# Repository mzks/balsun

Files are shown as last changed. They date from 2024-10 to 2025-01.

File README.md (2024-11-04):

# balsun - Balloon adaptive link board with Wi-SUN

This is an arduino-compatible board for balloon experiments.

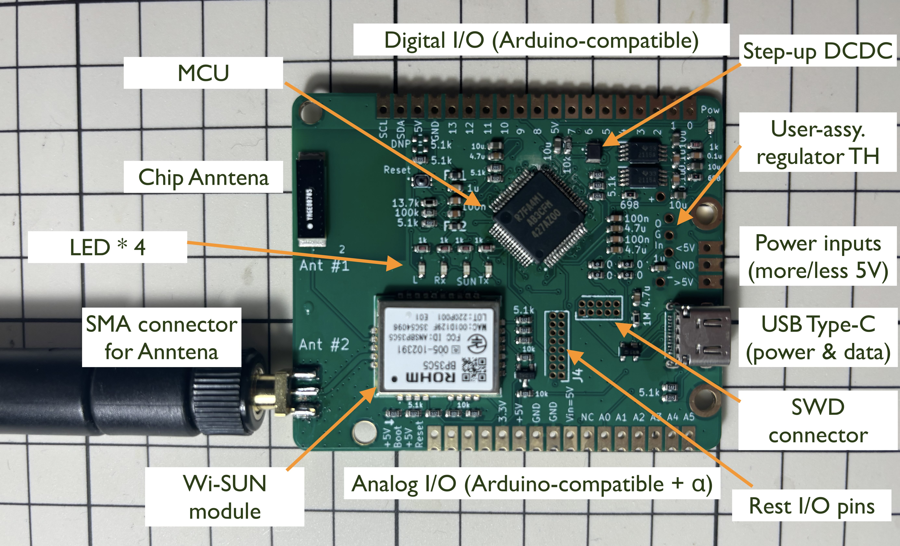
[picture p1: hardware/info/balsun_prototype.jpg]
Balsun prototype photo


## Features

 - Arduino UNO R4 Minima-compatible hardware
 - Low EMC noise for general balloon RF system
 - Wi-SUN FAN communication (MIC/TELEC, FCC)
 - Open hardware and software

## Specifications

 - MCU Renesas RA4M1
 - 5V IOs (GPIO, UART, SCI, I2C, CAN, ADC, DAC, OpAmp) with castellated holes
 - Write bootloader/sketch/program via USB type-C
 - Multi power sources (1.5--5V) and more (users can mount their regurator via through holes)
 - PCB size is 64.5 * 53.4 mm, FR-4 1.6 mm
 - Wi-SUN with BP35C5 (RoHM) and two types of the anntena

## How can I get?

All hardware design is published as KiCAD files.
You can ask some manifactures to build them.
If you are customer of JLCPCB, Elecrow, FusionPCB, or PCBWay, you can find the zip files including everything to build PCB in [here](/hardware/info/gerber_to_order).
For PCBA, BOM and Pos files are [here](/hardware/info).
All parts are available in Mouser (2024 Oct. 24).

## Contact
Keita Mizukoshi (mizukoshi.keita@jaxa.jp)

## Local information
Japanese specific information and discussion among local balloon community in [jp-docs](/docs/jp-docs.md).

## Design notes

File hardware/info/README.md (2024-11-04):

# Hardware design documents

  - [Circuit diabram / 回路図](circuit_diagram.pdf) -- pdf内マウスオーバーで詳細情報あり
  - [BOM / 部品リスト](BOM_grouped.csv)
  - [Gerber files to order / PCB製造業者毎のガーバーファイルなど](gerber_to_order)

  - [ボードのイメージ図](board_top.png)
  - [部品リスト(未グループ化)](BOM.csv)
  - [部品位置 (top)](balsun-top.pos)
  - [部品位置 (bottom)](balsun-bottom.pos) -- 下側に実装するSMDはなし
  - [Simple CAD model / ボードのCADモデル](cad_model.step)
  - [P板.comに依頼した際の部品調達書](BOM_pban.xlsx)

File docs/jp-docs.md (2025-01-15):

# Balsun 国内向け情報

## Balsun
Balsun - Balloon adaptive link board with Wi-SUN は, 大気球実験向けに作ったWi-SUNチップを搭載したArduino UNO R4 Minima 互換ボードです.
大気球実験PIが, 地上系/搭載系で簡単に用いることができる汎用ボードとして開発されています.
なお, 開発者や開発者の所属機関が性能を保証する性質のものではありません.

## 今後
現在アルファ版作成の準備として製作業者の選定, 依頼を進めています.

## Getting started
Arduinoとして使う方法を説明します.
これらは, 試験用の仮の方法であり, 将来的に更新される予定です.

### ブートローダーの書き込み
[こちら](https://zenn.dev/ichirowo/articles/6aa1614e102bce) も参考になります.

まずは, USBの接続状態を確認できるツールをインストールします.
例えば, [USB Device Tree Viewer](https://www.uwe-sieber.de/usbtreeview_e.html) が利用できます.

次に, [Renesas Flash Programmer](https://www.renesas.com/jp/ja/software-tool/renesas-flash-programmer-programming-gui#overview) をダウンロード, インストールします.

最後に, [Arduino IDE](https://www.arduino.cc/en/software) をインストールして, Arduino UNO R4 Minimaのための設定をしておきます.

Balsun基板の, Boot pin (左下から2番目) とGNDをショートして, USB type-C経由でコンピューターと接続します.
その後, Resetボタンをおす (または, Reset pinとGNDのショート) と, デバイスが認識されます.
USB Device Tree Viewerに, RA USB Boot(CDC)(COMxx) などと表示されます.

Renesas Flash Programmerを起動して, ファイル→新しいプロジェクトを作成を選択し, マイクロコントローラにRA, COM portに確認したポートを指定します. その他は適当に入力してください.
または, "Connect Settings" タブからToolに COM port, Speedに115200 bps, Tool Details... に確認したCOMポートを指定します.

プログラムファイルの「参照」をクリックし、UNO R4 MINIMAのブートローダーを指定します。以下のフォルダから、「`dfu_minima.hex`」を指定します。
`C:\Users\<ユーザー名>\AppData\Local\Arduino15\packages\arduino\hardware\renesas_uno\1.0.1\bootloaders\SANTIAGO`
もしくは
`C:\Users\<ユーザー名>\AppData\Local\Arduino15\packages\arduino\hardware\renesas_uno\1.0.2\bootloaders\UNO_R4`

スタートボタンをおすと, 書き込みが始まります. 緑色で"操作が成功しました"と表示されたら完了です.

その後, Arduino IDEを開いて, 適当なスケッチを書き込めが, Arduinoとして認識されるはずです.

### Wi-SUNチップの利用

以下のスケッチをMaster, Slaveにそれぞれ書き込みます.

 - master
 ```
UART SerialX(23,24);

void setup() {

  pinMode(LED_BUILTIN, OUTPUT);
  Serial.begin(9600); // USB type-C
  SerialX.begin(115200, SERIAL_8N1); // Serial pin for Wi-SUN
    
  R_IOPORT_PinCfg(NULL, BSP_IO_PORT_02_PIN_04, IOPORT_CFG_PORT_DIRECTION_OUTPUT);

  R_IOPORT_PinWrite(NULL, BSP_IO_PORT_02_PIN_04, BSP_IO_LEVEL_HIGH);
  delay(100);
  R_IOPORT_PinWrite(NULL, BSP_IO_PORT_02_PIN_04, BSP_IO_LEVEL_LOW);
  delay(100);
  R_IOPORT_PinWrite(NULL, BSP_IO_PORT_02_PIN_04, BSP_IO_LEVEL_HIGH);
  delay(100);
  SerialX.println ("atstart BORDER");
  delay(100);
  SerialX.println("save");
  delay(100);
  SerialX.println("vernum");
  delay(10000);
  SerialX.println("rantsw 1"); // 1 for chip, 2 for SMA
  delay(100);

  digitalWrite(LED_BUILTIN, HIGH);
  //if (SerialX.available() > 0){
  //  String msg = SerialX.readString();
  //  Serial.print(msg);
  //} 
}

const int adc_pin = A5;
int counter = 0;

void loop() {
  if (Serial.available() > 0){
    String cmd = Serial.readString();
    SerialX.print(cmd);
  }
  if (SerialX.available() > 0){
    String msg = SerialX.readString();
    Serial.print(msg);
  } 

  counter++;

  delay(100);
}

 ```

 - slave
 ```
 UART SerialX(23, 24);

int split(String data, char delimiter, String* dst) {
  int index = 0;
  int arraySize = (sizeof(data)) / sizeof((data[0]));
  int datalength = data.length();

  for (int i = 0; i < datalength; i++) {
    char tmp = data.charAt(i);
    if (tmp == delimiter) {
      index++;
      if (index > (arraySize - 1)) return -1;
    } else dst[index] += tmp;
  }
  return (index + 1);
}

int pin2_counter = 0;
int pin3_counter = 0;
int pin4_counter = 0;

void setup() {

  pinMode(2, OUTPUT);
  pinMode(3, OUTPUT);
  pinMode(4, OUTPUT);

  Serial.begin(9600); // USB type-C

  SerialX.begin(115200, SERIAL_8N1); // Serial pin for Wi-SUN

  R_IOPORT_PinCfg(NULL, BSP_IO_PORT_02_PIN_04, IOPORT_CFG_PORT_DIRECTION_OUTPUT);

  R_IOPORT_PinWrite(NULL, BSP_IO_PORT_02_PIN_04, BSP_IO_LEVEL_HIGH);
  delay(100);
  R_IOPORT_PinWrite(NULL, BSP_IO_PORT_02_PIN_04, BSP_IO_LEVEL_LOW);
  delay(100);
  R_IOPORT_PinWrite(NULL, BSP_IO_PORT_02_PIN_04, BSP_IO_LEVEL_HIGH);
  delay(100);

  delay(10000);
  SerialX.println("rantsw 1"); // 1 for chip, 2 for SMA
}

int counter = 0;
const int adc_pin = A5;

void loop() {
  if (Serial.available() > 0){
    String cmd = Serial.readString();
    SerialX.print(cmd);
  }

  if (SerialX.available() > 0){
    String msg = SerialX.readString();
    Serial.print(msg);

    int idx = msg.indexOf("tcpr");

    if(idx == 1){
      String buf[10];
      split(msg, ' ', buf);
      int cmdid = buf[2].toInt();

      if(cmdid==1){
          Serial.print("debug command");
          SerialX.println("tcps 2001:db8::1 0000");
      } else if (cmdid==2){
        SerialX.println("tcps 2001:db8::1 0002");
        pin2_counter = 300;
        digitalWrite(2, HIGH);
      } else if (cmdid==3){
        SerialX.println("tcps 2001:db8::1 0003");
        pin3_counter = 300;
        digitalWrite(3, HIGH);
      } else if (cmdid==4){
        SerialX.println("tcps 2001:db8::1 0004");
        pin4_counter = 100;
        digitalWrite(4, HIGH);
      } else if (cmdid==9){
        pin2_counter = 0;
        pin3_counter = 0;
        pin4_counter = 0;
        digitalWrite(4, HIGH);
      } else if (cmdid==9999){
          digitalWrite(2, HIGH);
          digitalWrite(3, HIGH);
          digitalWrite(4, HIGH);
          delay(10000);
          digitalWrite(2, LOW);
          digitalWrite(3, LOW);
          digitalWrite(4, LOW);
      }
    }

  }
  if (pin2_counter>0){pin2_counter--;} else {digitalWrite(2, LOW);}
  if (pin3_counter>0){pin3_counter--;} else {digitalWrite(3, LOW);}
  if (pin4_counter>0){pin4_counter--;} else {digitalWrite(4, LOW);}

  if (counter % 1000 == 999){
    int adc = analogRead(adc_pin);
    char sendPacket[24] = "";
    sprintf(sendPacket, "tcps 2001:db8::1 %04d", adc);
    SerialX.println(sendPacket);
    counter = 0;
  }

  counter++;
  delay(100);
}

 ```

書き込んだら, slaveの電源を投入し, masterはusbでコンピューターに接続してシリアルモニタを開きます.
ボーレートは9600です. (Source codeをいじれば適当に変えられます.)

```
atstart BORDER
```
とすると, response `atstart 1(BORDER)` が帰ってくるはずです.
これで, 設定をRAMに書き込むために, `save` と書き込むと, `save parameter is saved` とResponseが帰ってくるはずなので,
`reset` を打ってWi-SUNのチップの再立ち上げをします.
以下の出力が見えるはずです.
```
18:44:34.164 -> reset delay 0sec
18:44:34.164 -> inf 01,01,0,0       {    WSN: system booted.                      }
18:44:34.164 ->
////////////////////////////////////////////////////////////
18:44:34.164 -> // Copyright (C) 2020 Nissin Systems Co.,Ltd.
18:44:34.164 -> // EW-WSN-FAN-1.0.56.60 ROHM BP35C5(ROHM ML7436N:ML7421)
18:44:34.164 -> // Wi-SUN Profile for FAN (Dec 24 2020 12:55:57)
18:44:34.164 -> ////////////////////////////////////////////////////////////
18:44:34.164 -> auto start 1 (BORDER)...
18:44:34.164 -> init 1(BORDER)
18:44:34.164 -> inf 2b,62,0,5       {   FMng: changed fan join state (0 -> 5)     }
```

しばらく待つと, Slave機器を認識して, addressを与えます.

```
18:44:34.164 -> >inf 40,2b,bb48,4f5  {   NBRS: added new neighbor <001d129f35c54096>}
nebr <001d129f35c54096>: 256/127(-47)	<::>
18:45:07.166 -> >
inf 40,2d,3f7f,bb48 {   NBRS: added address <2001:db8::a9> to <001d129f35c54096>}
18:45:22.104 -> >
inf 4c,39,9d8c,9d60 {    RPL: added node <2001:db8::a9> => <2001:db8::1>}

```
その後, SlaveはADCの値を読んで定期的にMasterと通信してくるので,
```
tcpr <2001:db8::a9> 0040
18:47:14.445 -> >
tcpr <2001:db8::a9> 0040
18:48:55.375 -> >
tcpr <2001:db8::a9> 0040
18:50:36.343 -> >
tcpr <2001:db8::a9> 0041
18:52:17.342 -> >
```
以下のような出力が見えるはずです.

コマンドの詳細はdocumentを参照してください.
将来的にはWrapperを準備するつもりです.

また, 上でslaveのアドレスを確認したら, Masterから通信することもできます.
例えば,
```
tcps 2001:db8::a9 0000
```
などとすると, ScriptにしたがってResponseがあるはずです.

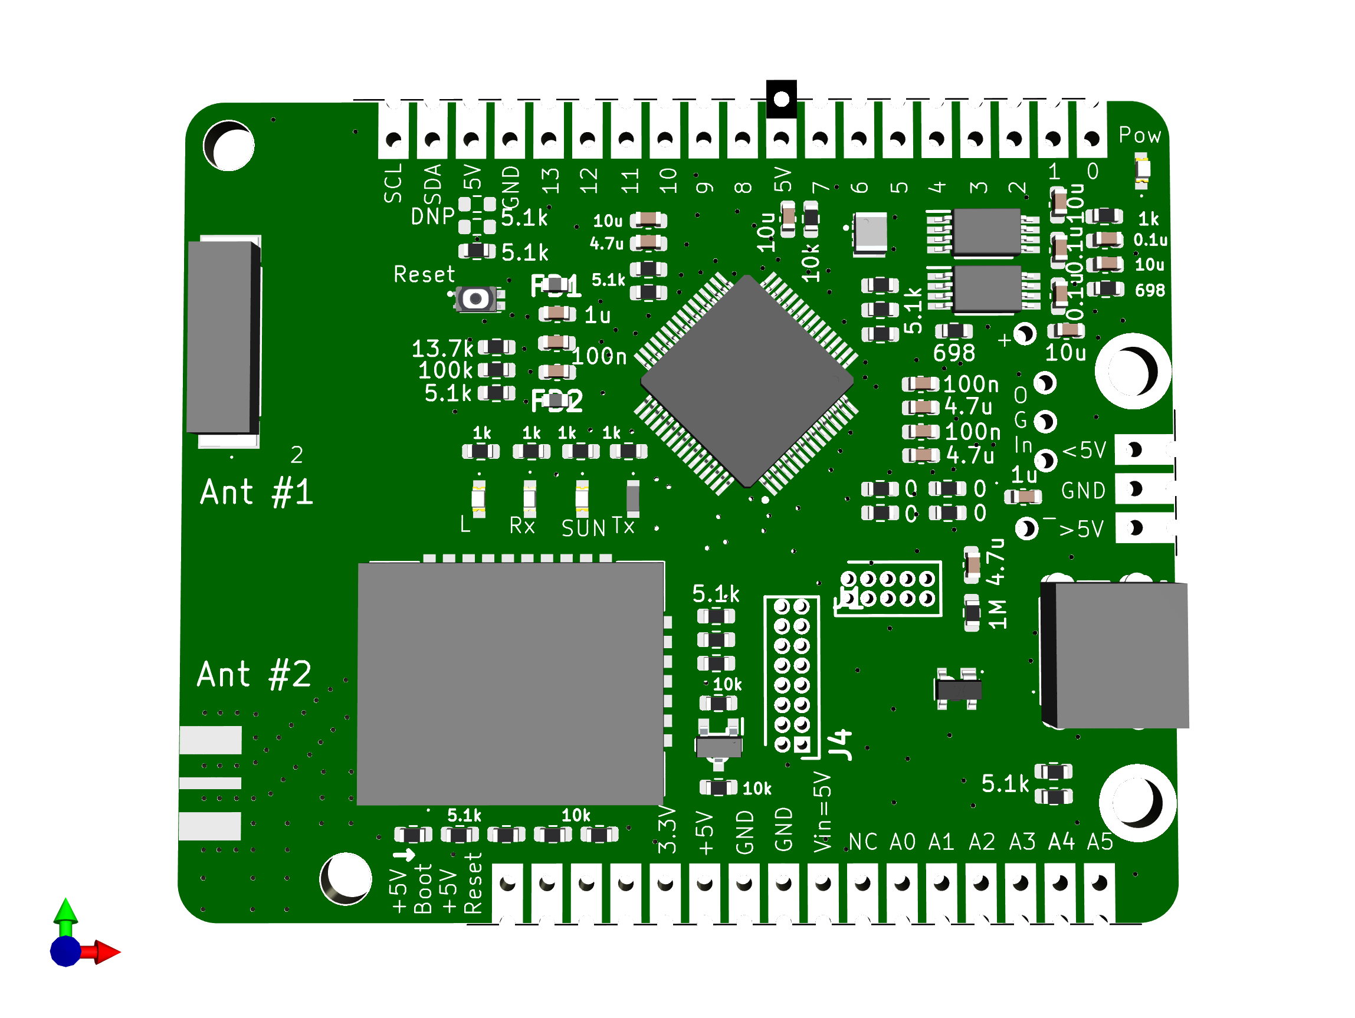
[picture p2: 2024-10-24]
hardware/info/board_top.png

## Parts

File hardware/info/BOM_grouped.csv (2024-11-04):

Reference | Value | Datasheet | Footprint | Qty | DNP | Manufacturer_Name | Manufacturer_Part_Number | Mouser Part Number | Mouser Price/Stock
ANT1 | ANT1204F005R0915A | https://eu.mouser.com/datasheet/2/447/datasheet_pulse_915mhz_1204_chip_antenna_type05_an-2903025.pdf | ANT1204F005R0915A | 1 |  | Pulse Electronics | ANT1204F005R0915A | 603-ANT1204F005R0915 | https://www.mouser.co.uk/ProductDetail/PulseLarsen-Antennas/ANT1204F005R0915A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
C1,C14 | 1u | ~ | Capacitor_SMD:C_0603_1608Metric | 2 |  |  |  | 603-CC603KRX5R6BB105
C2,C5,C7,C8 | 100n | ~ | Capacitor_SMD:C_0603_1608Metric | 4 |  |  |  | 603-CC603KRX7R6BB104
C3,C6,C9,C10 | 4.7u | ~ | Capacitor_SMD:C_0603_1608Metric | 4 |  |  |  | 603-CC603ZRY5V6BB475
C4,C11,C12,C13,C16 | 10u | ~ | Capacitor_SMD:C_0603_1608Metric | 5 |  |  |  | 603-CC603MRX6S6BB106
C15,C17,C18 | 0.1u | ~ | Capacitor_SMD:C_0603_1608Metric | 3 |  |  |  | 603-CC603KRX7R6BB104
D1 | PRTR5V0U2X,215 | https://assets.nexperia.com/documents/data-sheet/PRTR5V0U2X.pdf | PRTR5V0U2X | 1 |  | Nexperia | PRTR5V0U2X,215 | 771-PRTR5V0U2X-T/R | https://www.mouser.co.uk/ProductDetail/Nexperia/PRTR5V0U2X215?qs=LOCUfHb8d9sDkgY4cRj8Lw%3D%3D
FB1,FB2 | BLM18PG471SN1D | http://www.murata.com/~/media/webrenewal/support/library/catalog/products/emc/emifil/c31e.ashx?la=en-gb | BLM18SP221SN1B | 2 |  | Murata Electronics | BLM18PG471SN1D | 81-BLM18PG471SN1D | https://www.mouser.co.uk/ProductDetail/Murata-Electronics/BLM18PG471SN1D?qs=EYzdjubb4S%2FN1Ip39GrHyg%3D%3D
H1,H2,H3,H4,H5,P1 | ~ |  | -- mixed values -- | 6 | DNP
IC1 | R7FA4M1AB3CFM#AA0 | https://www.renesas.com/document/dst/renesas-ra4m1-group-datasheet?language=en&r=1054146 | QFP50P1200X1200X170-64N | 1 |  | Renesas Electronics | R7FA4M1AB3CFM#AA0 | 968-7FA4M1AB3CFM#AA0 | https://www.mouser.co.uk/ProductDetail/Renesas-Electronics/R7FA4M1AB3CFMAA0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
IC2 | BP35C5 | https://fscdn.rohm.com/en/products/databook/datasheet/module/power_module/specified_low_power/bp35c5-e.pdf | BP35C5 | 1 |  | ROHM Semiconductor | BP35C5 | 755-BP35C5
IC3 | BP5293-50 | https://componentsearchengine.com/Datasheets/2/MC7805BDTRKG.pdf | SamacSys_Parts:BP5293-50 | 1 | DNP |  |  |  | https://www.mouser.co.uk/ProductDetail/onsemi/MC7805BDTRKG?qs=%252B9%2Fcbd0IE0RVSCV5SBH6%2FA%3D%3D
IC4 | XCL103D503CR-G | https://www.torexsemi.com/file/xcl102/XCL102-103.pdf | XCL103D503CRG | 1 |  | Torex | XCL103D503CR-G | 865-XCL103D503CR-G | https://www.mouser.co.uk/ProductDetail/Torex-Semiconductor/XCL103D503CR-G?qs=gt1LBUVyoHmrRO29mARr4A%3D%3D
IC5,IC6 | TPS2115APW | http://www.ti.com/lit/ds/symlink/tps2115a.pdf | SOP65P640X120-8N | 2 |  | Texas Instruments | TPS2115APW | 595-TPS2115APW | https://www.mouser.co.uk/ProductDetail/Texas-Instruments/TPS2115APW?qs=ojKcPFmCWSV6g5xXyJEDWQ%3D%3D
J1 | HPH2-A-10-UA |  | HDRV10W45P127_2X5_635X345X400P | 1 | DNP | Adam Tech | HPH2-A-10-UA | 737-HPH2-A-10-UA
J2,J4 | 61301611821 | https://www.we-online.com/catalog/datasheet/61301611821.pdf | -- mixed values -- | 2 | DNP | Wurth Elektronik | 61301611821 | 710-61301611821 | https://www.mouser.co.uk/ProductDetail/Wurth-Elektronik/61301611821?qs=xZ%2FP%252Ba9zWqYIxo6RU%252B1Wuw%3D%3D
J5 | CX90B2-24P | https://www.hirose.com/en/product/document?clcode=CL0480-0889-0-00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 | CX90B224P | 1 |  | Hirose | CX90B2-24P | 798-CX90B2-24P
J6 | SMA-J-P-H-RA-TH1 | https://www.we-online.com/components/products/datasheet/63012202124505.pdf | SamacSys_Parts:CON-SMA-EDGE-S | 1 | DNP | SAMTEC | SMA-J-P-H-RA-TH1 | 710-63012202124505
L1,L2,L3,L4,L5 | SML-P11UTT86 | https://fscdn.rohm.com/en/products/databook/datasheet/opto/led/chip_mono/smld12en1wt86(c)-e.pdf | -- mixed values -- | 5 |  | ROHM Semiconductor | SML-P11UTT86 | 755-755-SML-P11UTT86 | https://www.mouser.co.uk/ProductDetail/ROHM-Semiconductor/SMLD12EN1WT86C?qs=Z%252BL2brAPG1KJHKBIKSy7wg%3D%3D
Q1 | BSS138 | https://www.onsemi.com/pub/Collateral/BSS138-D.PDF | SOT95P240X120-3N | 1 |  | onsemi | BSS138 | 512-BSS138 | https://www.mouser.co.uk/ProductDetail/onsemi-Fairchild/BSS138?qs=HK%252BeIG1iaahCeqBvjB4arg%3D%3D
R1,R4,R5,R8,R11,R13,R16,R19,R20,R21,R22,R23,R24,R25,R26 | 5.1k | ~ | Resistor_SMD:R_0603_1608Metric | 15 |  |  |  | 667-ERA-3ARB512V
R2,R3 | 5.1k | ~ | Resistor_SMD:R_0603_1608Metric | 2 | DNP |  |  | 667-ERA-3ARB512V
R6 | 100k | ~ | Resistor_SMD:R_0603_1608Metric | 1 |  |  |  | 667-ERA-3AEB104V
R7 | 13.7k | ~ | Resistor_SMD:R_0603_1608Metric | 1 |  |  |  | 667-ERA-3AEB1372V
R9,R10,R14,R15,R32 | 10k | ~ | Resistor_SMD:R_0603_1608Metric | 5 |  |  |  | -- mixed values --
R12 | 1M | ~ | Resistor_SMD:R_0603_1608Metric | 1 |  |  |  | 667-ERJ-3EKF1004V
R18,R34,R35,R36 | 0 | ~ | Resistor_SMD:R_0603_1608Metric | 4 |  |  |  | 667-ERJ-3GEY0R00V
R27,R28,R29,R30,R31 | 1k | ~ | Resistor_SMD:R_0603_1608Metric | 5 |  |  |  | 667-ERJ-U03J331V
R33,R37 | 698 | ~ | Resistor_SMD:R_0603_1608Metric | 2 |  |  |  | 667-ERA-3AEB6980V
S2 | EVP-BB2A9B000 | https://industrial.panasonic.com/ac/cdn/e/control/switch/light-touch/catalog/sw_lt_eng_2616s.pdf | SamacSys_Parts:EVPBB2A9B000 | 1 |  | Panasonic | EVP-BB2A9B000 | 667-EVP-BB2A9B000 | https://www.mouser.co.uk/ProductDetail/Panasonic/EVP-BB2A9B000?qs=iHX4uCgIbgPa3HqgzZ6vLw%3D%3D
U1 | 2479 | http://www.keyelco.com/product-pdf.cfm?p=1041 | 2479 | 1 | DNP | Keystone Electronics | 2479 | 534-2479 | https://www.mouser.co.uk/ProductDetail/Keystone-Electronics/2479?qs=Q3RoVmURDomBPD85HfXZoA%3D%3D

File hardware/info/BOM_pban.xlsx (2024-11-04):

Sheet: 必ずお読みください
入力項目説明
メ ー カ ー |  |  | 電子部品のメーカー名をご入力ください。
部 品 種 別 |  |  | 電子部品の種別をご入力ください。例：チップ抵抗、トランジスタ、LED、など
電 子 部 品 型 番 |  |  | 電子部品の型番をご入力ください。 ※誤表記による不具合を回避するためにも正確なご入力をお願い致します。 ※表面実装の抵抗やコンデンサ(電解、タンタル以外)は、後述「電子部品見取り表」をご参照のうえ、ご入力ください。
配 置 記 号 / リファレンス |  |  | シルク図/配置図に表記された配置記号/リファレンス番号をご入力ください。 ※複数入力する場合は、カンマ「,」区切りでのご入力をお願い致します。 (入力例)R1～R5、R1-5と略さず、R1,R2,R3,R4,R5とご入力ください。 ※電子部品型番ベースでのご記入をお願い致します。（１つの電子部品型番に対して、配置番号を複数記入）
個 数 |  |  | 電子部品の個数をご入力ください。
ピ ン 数 |  |  | 電子部品の総ピン数をご入力ください。 ※基板取付穴、部品取付穴、全てのスルー・ノンスルーホール、面実装部品のパッド、及び次の①～⑤の配線を伴う箇所（①テストピン、②チェックランド、③引き出しランド、④ジャンパピン、⑤入出力ランドの総計。
実装 / 未実装 |  |  | 実装サービスでの「実装」/「未実装」をご選択ください。 ※同じ電子部品型番の中で実装と未実装が分かれる場合は、それぞれ2行に分けて配置記号をご入力ください。
部品分類 | SMD |  | 表面実装部品
 | DIP |  | 挿入部品
 | 特殊 BGA等 |  | BGA/CSP/LGA/QFNなど部品極性が部品の真下に配置された部品 -BGA：Ball Grid Array/下面に半田ボールの端子を配置したパッケージ。 -CSP：Chip Size Package/チッププサイズと同じか、もしくは僅かに大きいパッケージ。 -LGA：Land Grid Array/裏面に外部入出力用のランドを設けたパッケージ。※BGAの半田ボールがない。 -QFN：Quad Flat Non-Lead Package/QFPに似ていますが、外部入出力用のピンが出ていないパッケージ。
P板.com提供部品 (無料) |  |  | 【無償提供部品一覧】シートに記載されている「メーカー型番」を【部品リスト入力フォーム】シートのD列（電子部品型番）に入力し、I列（実装／未実装）を「実装」に設定いただくと、自動的に「○」が表示されます。 ※無料提供部品：チップコンデンサ/チップ抵抗を約1000種、実装サービスをご利用のお客様に無料提供いたします。 ※「○」が付かない場合は全半角の不一致などにより誤判定されている可能性があります。【無償提供部品一覧】シートより型番をコピー＆ペーストにて【部品リスト入力フォーム】にご入力ください。
 |  |  | http://www.p-ban.com/implementation/chip.html
P板.com調達部品(有料） |  |  | P板.com実装サービスで部品調達を希望される場合に○をご選択ください。 ※調達費用のお見積もりは、部品リストの返却と同時にご連絡いたします。 ※ご希望の納期や市場在庫状況によっては、調達が不可となる部品もございますので、予めご了承ください。
パッケージ情報 部品外形/部品仕様 |  |  | 電子部品のパッケージ情報をご入力ください。例：1608 , DIP , 0.5mmピッチQFP , 0.4mmピッチCN
データシートURL |  |  | 必要に応じて部品データシートのURLをご入力ください。
コ メ ン ト |  |  | 特別なご指示のある電子部品について、自由にご入力ください。 例：未実装挿入穴のマスク処理が必要、など
版、変更履歴 |  |  | 部品種毎に、変更履歴を記載してください。 版は、アカウント登録の版に合わせて記載ください。
調達型式、代替型式 |  |  | 無料提供部品の在庫切れや、正確な調達型式を記載いたします。
部品名称見取り表
1.チップ部品（抵抗、コンデンサ）
 |  |  |  |  | 単位：ｍｍ
 |  |  | 電子部品型番 (C:コンデンサ、R:抵抗） | Ａ寸法 | Ｂ寸法
 |  |  | C/R1608 | 1.6 | 0.8
 |  |  | C/R2125 | 2 | 1.25
 |  |  | C/R3216 | 3.2 | 1.6
 |  |  | C/R3225 | 3.2 | 2.5
 |  |  | C/R4532 | 4.5 | 3.2
2.チップタンタルコンデンサ
 |  |  |  |  | 単位：ｍｍ
 |  |  | 電子部品型番 | Ａ寸法 | Ｂ寸法
 |  |  | CT3216 | 3.2 | 1.6
 |  |  | CT3528 | 3.5 | 2.8
 |  |  | CT4726 | 4.7 | 2.6
 |  |  | CT6032 | 6 | 3.2
 |  |  | CT5846 | 5.8 | 4.6
 |  |  | CT7343 | 7.3 | 4.3
3.チップアルミ電解コンデンサ
 |  |  |  |  |  | 単位：ｍｍ
 |  |  | 電子部品型番 | Ａ寸法 | Ｂ寸法 | C寸法
 |  |  | CE33 | 3.3 | 3.3 | φ3.0
 |  |  | CE43 | 4.3 | 4.3 | φ4.0
 |  |  | CE53 | 5.3 | 5.3 | φ5.0
 |  |  | CE66 | 6.6 | 6.6 | φ6.3
 |  |  | CE83 | 8.3 | 8.3 | φ8.0
 |  |  | CE103 | 10.3 | 10.3 | φ10.0
部品取り付け穴は、ピン数に含めてください。
コネクタの場合 |  |  |  |  |  | トランスの場合
部品リストフォーマット変更履歴
2014-02-01 | v2.0 | 松森 | 部品種別の総計を、直接関数に変更
 |  |  | ピン数合計、実装数合計数量を、直接関数に変更
 |  |  | 部品調達見積欄を修正
2014-03-11 | v2.1 | 松森 | *N列、O列が下の方、"○"選択リスト消えていたのを追加
 |  |  | *縮小しても解像度崩れず文字表示するため、フォントを"Meiryo UI"(Windows 標準添付)に変更
 |  |  | *136行目以降を非表示
 |  |  | *"X"列にリストを埋め込み
2014-06-12 | v2.2 | 松森 | *固定行を変更
 |  |  | *在庫状況列に条件付き書式設定
 |  |  | *その他各種バグ修正
2015-03-31 | V2.3 | 松森 | *無償提供部品を記載すると、無償提供部品欄に自動で"○"が表示されるよう条件式を挿入
 |  |  | *併せて、無償提供部品参照用一覧シートの作成・追加
 |  |  | *最小購入数が必要数量を下回る場合、セルを赤色にハッチングする
 |  |  | *シート1の名称変更
 |  |  | *変更履歴シートの追加
2015-06-19 | v2.4 | 松森 | ・ゼロΩ抵抗を無償対象に追加
 |  |  | ・変更履歴の列を追加し、変更履歴シートを削除
 |  |  | ・その他書式、印刷機能の変更
 |  |  | ・無償提供部品の入れ替え
2015-08-14 | v2.5 | 松森 | ・ゼロΩ抵抗の無償対象品が正しく反映されていなかったバグ修正
 |  |  | ・フォームへバージョン情報を埋め込み
2015-11-05 | v2.6 | 上田 | ・無償提供部品(RK73H2ATTD1601F)の抵抗値を正しい値に修正
2015-11-09 | v2.7 | 上田 | ・P板.com調達部品(無料)欄のフォントを変更
2016-01-15 | v2.8 | 箕浦 | ・無償提供部品一覧の「GRM32NF11E106Z」を削除
 |  |  | ・部品リスト入力フォームの4行目F列～L列の計算式が136行目以降を対象としていなかった不具合を修正
2016-01-27 | v2.9 | 箕浦 | ・「無償提供部品一覧」シートの表記修正
2016-08-26 | v2.10 | 松森 | ・「GRM31CF11E106Z」の許容差値修正
2016-11-15 | v2.11 | 松森 | ・部品調達欄表示順序変更
 |  |  | ・備考欄、荷姿欄追加
 |  |  | ・在庫状況のリスト微修正
2017-03-21 | v2.12 | 松森 | ・調達金額合計欄作成
 |  |  | ・在庫状況「長納期」を追加
 |  |  | ・その他微修正
2017-06-29 | v2.13 | 松森 | ・村田製3216サイズ以上のチップコンの取扱い中止
2017-07-19 | V2.14 | 松森 | ・KOA製1005サイズの定格電力を0.1Wに変更
 |  |  | (2015年10月のKOA仕様変更に伴う)
2017-09-14 | v2.15 | 松森 | ・KOA製2012サイズの定格電力を0.25Wへ変更
 |  |  | ・KOA製1608サイズ、1K以下の定格電力を0.125Wへ変更
 |  |  | ・MURATA製一部型式、許容差および定格修正
 |  |  | ・MURATA製一部部品削除
 |  |  | ・その他書式設定等微修正
2017-10-12 | v2.20 | 松森 | ・部品調達関連項目の移動
 |  |  | ・条件付き書式追加
2018-06-22 | v2.31 | 松森 | ・「1608」サイズと「2012」サイズのチップコンデンサを無償対象品から除外
2018-10-18 | V2.32 | 山田 | ・部品調達関連項目追加（条件付き書式追加/在庫状況：在庫少追加）
 |  |  | ・「必ずお読みください」シートの「配置記号 / リファレンス」の項目修正（配置記号の省略について）
2019-09-05 | V2.4 | 岡田 | Excelファイル名を部品表内に表記する関数追加
 |  |  | 無償提供部品型番入力後にスペースが入るとO列に丸がされない問題を修正
2019-09-10 | V2.41 | 岡田 | "AD"列にトレイ追加
2019-11-27 | V2.42 | 岡田 | D列に0(ゼロ)から始まる型番を入力すると先頭の0が消えてしまう問題あり
 |  |  | Excelの表示形式を標準から文字列に変更して問題を修正
2023-04-17 | V2.43 | 宮坂 | 「配置記号リファレンス」に対して、行の高さの自動設定を適用
2024-06-24 | V2.44 | 尾城 | 入力可能行数を変更（148行→255行）
2023-06-24 | V2.45 | 尾城 | ・データシートURL欄追加

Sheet: 10台
partslist(Rev,2.45) |  |  | 電 子 部 品 型 番 ※半角英数字 ※サフィックスまで入力必須 | 配 置 記 号 リ フ ァ レ ン ス ※半角英数字） | 個数 | ピ ン 数 (部品取付穴 を含む） |  | 実装/ 未実装 | 部 品 分 類 |  |  | 必要数 実装枚数を入れてください。 ↓ | P板.com 提供 部品 (無料) | P板.com 調達 部品 (有料） | パッケージ情報 部品外形/部品仕様 | データシートURL | コ メ ン ト ※未実装挿入穴のマスク 処理が必要、など | 版 変更履歴 | 入荷数 | 返却 | 見積NO. | 202410240029G | 2024-10-31 | 管理番号 | PM10389
202410240029G_BOM_grouped_回答2版1031.xlsx
No | メーカー | 部品種別 |  |  |  | 1個 あたり | 合計 | 実装個数 | SMD | DIP | 特殊 BGA等 |  |  |  |  |  |  |  |  |  | P板.com部品調達使用欄
 |  |  |  |  | 83 | 190 | 288 | 69 | 67 | 0 | 2 | 10 | リスト (http://www.p-ban.com/implementation/chip.html)
例 | KOA | チップ抵抗 | RK73B2ATTD1002F | R1,R5,R9,R10 | 4 | 2 | 8 | 未実装 | SMD |  |  |  |  |  | 2012 |  |  | 4版 型式訂正、個数変更、 実装→未実装へ |  |  | 必要数 | 調達数 | 在庫状況 | メーカ | 調達品番 | 荷姿 | 納期 | 備考
1 □ | Pulse Electronics | チップアンテナ | ANT1204F005R0915A | ANT1 | 1 | 2 | 2 | 実装 | SMD |  |  | 10 |  | ○ | SMD | https://eu.mouser.com/datasheet/2/447/datasheet_pulse_915mhz_1204_chip_antenna_type05_an-2903025.pdf | 603-ANT1204F005R0915 |  |  | □ | 10 | 11 | 有り |  |  | ﾐﾆﾘｰﾙ | 2W
2 □ | YAGEO | チップキャパシタ | CC603KRX5R6BB105 | C1,C14 | 2 | 2 | 4 | 実装 | SMD |  |  | 20 |  | ○ | 1608 | ~ | 603-CC603KRX5R6BB105 |  |  | □ | 20 | 21 | 調達型式 | YAGEO | CC0603KRX5R6BB105 | ﾐﾆﾘｰﾙ | 2W
3 □ | YAGEO | チップキャパシタ | CC603KRX7R6BB104 | C2,C5,C7,C8 | 4 | 2 | 8 | 実装 | SMD |  |  | 40 |  | ○ | 1608 | ~ | 603-CC603KRX7R6BB104 |  |  | □ | 40 | 100 | 調達型式 | YAGEO | CC0603KRX7R6BB104 | ﾐﾆﾘｰﾙ | 2W
4 □ | YAGEO | チップキャパシタ | CC603ZRY5V6BB475 | C3,C6,C9,C10 | 4 | 2 | 8 | 実装 | SMD |  |  | 40 |  | ○ | 1608 | ~ | 603-CC603ZRY5V6BB475 |  |  | □ | 40 | 42 | 調達型式 | YAGEO | CC0603ZRY5V6BB475 | ﾐﾆﾘｰﾙ | 2W
5 □ | YAGEO | チップキャパシタ | CC603MRX6S6BB106 | C4,C11,C12,C13,C16 | 5 | 2 | 10 | 実装 | SMD |  |  | 50 |  | ○ | 1608 | ~ | 603-CC603MRX6S6BB106 |  |  | □ | 50 | 52 | 調達型式 | YAGEO | CC0603MRX6S6BB106 | ﾐﾆﾘｰﾙ | 2W
6 □ | YAGEO | チップキャパシタ | CC603KRX7R6BB104 | C15,C17,C18 | 3 | 2 | 6 | 実装 | SMD |  |  | 30 |  | ○ | 1608 | ~ | 603-CC603KRX7R6BB104 |  |  | □ | 30 | No.3 に含まれる | 調達型式 | YAGEO | CC0603KRX7R6BB104 | ﾐﾆﾘｰﾙ | 2W
7 □ | Nexperia | ESD保護ダイオード | PRTR5V0U2X,215 | D1 | 1 | 4 | 4 | 実装 | SMD |  |  | 10 |  | ○ | TO-253-4 | https://assets.nexperia.com/documents/data-sheet/PRTR5V0U2X.pdf | 771-PRTR5V0U2X-T/R |  |  | □ | 10 | 11 | 有り |  |  | ﾐﾆﾘｰﾙ | 2W
8 □ | Murata Electronics | フェライトビーズ | BLM18PG471SN1D | FB1,FB2 | 2 | 2 | 4 | 実装 | SMD |  |  | 20 |  | ○ | 1608 | http://www.murata.com/~/media/webrenewal/support/library/catalog/products/emc/emifil/c31e.ashx?la=en-gb | 81-BLM18PG471SN1D |  |  | □ | 20 | 21 | 有り |  |  | ﾐﾆﾘｰﾙ | 2W
9 □ |  | ピンヘッダ | ~ | H1,H2,H3,H4,H5,P1 | 6 |  | 0 | 未実装 | DIP |  |  | 0 |  |  |  |  |  |  |  | □
10 □ | Renesas Electronics | マイクロコントローラ | R7FA4M1AB3CFM#AA0 | IC1 | 1 | 64 | 64 | 実装 | SMD |  |  | 10 |  | ○ | 64-LFQFP | https://www.renesas.com/document/dst/renesas-ra4m1-group-datasheet?language=en&r=1054146 | 968-7FA4M1AB3CFM#AA0 |  |  | □ | 10 | 10 | 有り |  |  | ﾄﾚｲ | 2W
11 □ | ROHM Semiconductor | Sub-GHz無線モジュール | BP35C5 | IC2 | 1 | 30 | 30 | 実装 | SMD |  |  | 10 |  | ○ | SMD | https://fscdn.rohm.com/en/products/databook/datasheet/module/power_module/specified_low_power/bp35c5-e.pdf | 755-BP35C5 |  |  | □ | 10 | 10 | 有り |  |  | ﾃｰﾌﾟｶｯﾄ | 2W
12 □ |  |  | ~ | IC3 | 1 |  | 0 | 未実装 |  |  |  | 0 |  |  |  | https://componentsearchengine.com/Datasheets/2/MC7805BDTRKG.pdf |  |  |  | □
13 □ | Torex | 昇圧DCDCコンバータ | XCL103D503CR-G | IC4 | 1 | 9 | 9 | 実装 | 特殊（BGA等） |  |  | 10 |  | ○ | 8-TDFN露出パッド | https://www.torexsemi.com/file/xcl102/XCL102-103.pdf | ****実装時ショートしないよう注意**** 865-XCL103D503CR-G |  |  | □ | 10 | 11 | 有り |  |  | ﾐﾆﾘｰﾙ | 2W
14 □ | Texas Instruments | 電源IC | TPS2115APW | IC5,IC6 | 2 | 8 | 16 | 実装 | SMD |  |  | 20 |  | ○ | 8-TSSOP | http://www.ti.com/lit/ds/symlink/tps2115a.pdf | 595-TPS2115APW |  |  | □ | 20 | 21 | 調達型式 | Texas Instruments | TPS2115APWR | ﾐﾆﾘｰﾙ | 2W
15 □ | Adam Tech | ピンヘッダ | HPH2-A-10-UA | J1 | 1 |  | 0 | 未実装 | DIP |  |  | 0 |  |  |  |  | 737-HPH2-A-10-UA |  |  | □
16 □ | Wurth Elektronik | ピンヘッダ | 61301611821 | J2,J4 | 2 |  | 0 | 未実装 | DIP |  |  | 0 |  |  |  | https://www.we-online.com/catalog/datasheet/61301611821.pdf | 710-61301611821 |  |  | □
17 □ | Hirose | USB type-Cコネクタ | CX90B2-24P | J5 | 1 | 32 | 32 | 実装 | 特殊（BGA等） |  |  | 10 |  | ○ | SMD, through hole | https://www.hirose.com/en/product/document?clcode=CL0480-0889-0-00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 | 798-CX90B2-24P |  |  | □ | 10 | 10 | 有り |  |  | ﾃｰﾌﾟｶｯﾄ | 2W
18 □ | SAMTEC | SMAコネクタ | SMA-J-P-H-RA-TH1 | J6 | 1 |  | 0 | 未実装 | 特殊（BGA等） |  |  | 0 |  |  |  | https://www.we-online.com/components/products/datasheet/63012202124505.pdf | 710-63012202124505 |  |  | □
19 □ | ROHM Semiconductor | LED | SML-P11UTT86 | L1,L2,L3,L4,L5 | 5 | 2 | 10 | 実装 | SMD |  |  | 50 |  | ○ | 1608 | https://fscdn.rohm.com/en/products/databook/datasheet/opto/led/chip_mono/smld12en1wt86(c)-e.pdf | 755-755-SML-P11UTT86 |  |  | □ | 50 | 52 | 有り |  |  | ﾐﾆﾘｰﾙ | 2W
20 □ | onsemi | FET | BSS138 | Q1 | 1 | 3 | 3 | 実装 | SMD |  |  | 10 |  | ○ | SOT-23-3 | https://www.onsemi.com/pub/Collateral/BSS138-D.PDF | 512-BSS138 |  |  | □ | 10 | 11 | 有り |  |  | ﾐﾆﾘｰﾙ | 2W
21 □ |  | チップ抵抗 | RK73H1JTTD5101F | R1,R4,R5,R8,R11,R13,R16,R19,R20,R21,R22,R23,R24,R25,R26 | 15 | 2 | 30 | 実装 | SMD |  |  | 150 | ○ |  | 1608 | ~ | 667-ERA-3ARB512V |  |  | □
22 □ |  | チップ抵抗 | RK73H1JTTD5101F | R2,R3 | 2 | 2 | 4 | 未実装 | SMD |  |  | 0 |  |  | 1608 | ~ | 667-ERA-3ARB512V |  |  | □
23 □ |  | チップ抵抗 | RK73H1JTTD1003F | R6 | 1 | 2 | 2 | 実装 | SMD |  |  | 10 | ○ |  | 1608 | ~ | 667-ERA-3AEB104V |  |  | □
24 □ | Panasonic | チップ抵抗 | ERA-3AEB1372V | R7 | 1 | 2 | 2 | 実装 | SMD |  |  | 10 |  | ○ | 1608 | ~ | 667-ERA-3AEB1372V |  |  | □ | 10 | 11 | 有り |  |  | ﾐﾆﾘｰﾙ | 2W
25 □ |  | チップ抵抗 | RK73H1JTTD1002F | R9,R10,R14,R15,R32 | 5 | 2 | 10 | 実装 | SMD |  |  | 50 | ○ |  | 1608 | ~ | -- mixed values -- |  |  | □
26 □ |  | チップ抵抗 | RK73H1JTTD1004F | R12 | 1 | 2 | 2 | 実装 | SMD |  |  | 10 | ○ |  | 1608 | ~ | 667-ERJ-3EKF1004V |  |  | □
27 □ |  | チップ抵抗 | RK73Z1JTTD | R18,R34,R35,R36 | 4 | 2 | 8 | 実装 | SMD |  |  | 40 | ○ |  | 1608 | ~ | 667-ERJ-3GEY0R00V |  |  | □
28 □ |  | チップ抵抗 | RK73H1JTTD1001F | R27,R28,R29,R30,R31 | 5 | 2 | 10 | 実装 | SMD |  |  | 50 | ○ |  | 1608 | ~ | 667-ERJ-U03J331V |  |  | □
29 □ |  | チップ抵抗 | RK73H1JTTD6800F | R33,R37 | 2 | 2 | 4 | 実装 | SMD |  |  | 20 | ○ |  | 1608 | ~ | 667-ERA-3AEB6980V |  |  | □
30 □ | Panasonic | スイッチ | EVP-BB2A9B000 | S2 | 1 | 4 | 4 | 実装 | SMD |  |  | 10 |  | ○ | SMD | https://industrial.panasonic.com/ac/cdn/e/control/switch/light-touch/catalog/sw_lt_eng_2616s.pdf | 667-EVP-BB2A9B000 |  |  | □ | 10 | 11 | 有り |  |  | ﾐﾆﾘｰﾙ | 2W
31 □ | Keystone Electronics | バッテリーボックス | 2479 | U1 | 1 | 2 | 2 | 未実装 | DIP |  |  | 0 |  |  | TH | http://www.keyelco.com/product-pdf.cfm?p=1041 | 534-2479 |  |  | □
32 □ |  |  |  |  |  |  |  |  |  |  |  |  |  |  |  |  |  |  |  | □
33 □ |  |  |  |  |  |  |  |  |  |  |  |  |  |  |  |  |  |  |  | □
34 □ |  |  |  |  |  |  |  |  |  |  |  |  |  |  |  |  |  |  |  | □
35 □ |  |  |  |  |  |  |  |  |  |  |  |  |  |  |  |  |  |  |  | □
36 □ |  |  |  |  |  |  |  |  |  |  |  |  |  |  |  |  |  |  |  | □
37 □ |  |  |  |  |  |  |  |  |  |  |  |  |  |  |  |  |  |  |  | □
38 □ |  |  |  |  |  |  |  |  |  |  |  |  |  |  |  |  |  |  |  | □
39 □ |  |  |  |  |  |  |  |  |  |  |  |  |  |  |  |  |  |  |  | □
40 □ |  |  |  |  |  |  |  |  |  |  |  |  |  |  |  |  |  |  |  | □
41 □ |  |  |  |  |  |  |  |  |  |  |  |  |  |  |  |  |  |  |  | □
42 □ |  |  |  |  |  |  |  |  |  |  |  |  |  |  |  |  |  |  |  | □
43 □ |  |  |  |  |  |  |  |  |  |  |  |  |  |  |  |  |  |  |  | □
44 □ |  |  |  |  |  |  |  |  |  |  |  |  |  |  |  |  |  |  |  | □
45 □ |  |  |  |  |  |  |  |  |  |  |  |  |  |  |  |  |  |  |  | □
46 □ |  |  |  |  |  |  |  |  |  |  |  |  |  |  |  |  |  |  |  | □
47 □ |  |  |  |  |  |  |  |  |  |  |  |  |  |  |  |  |  |  |  | □
48 □ |  |  |  |  |  |  |  |  |  |  |  |  |  |  |  |  |  |  |  | □
49 □ |  |  |  |  |  |  |  |  |  |  |  |  |  |  |  |  |  |  |  | □
50 □ |  |  |  |  |  |  |  |  |  |  |  |  |  |  |  |  |  |  |  | □
51 □ |  |  |  |  |  |  |  |  |  |  |  |  |  |  |  |  |  |  |  | □
52 □ |  |  |  |  |  |  |  |  |  |  |  |  |  |  |  |  |  |  |  | □
53 □ |  |  |  |  |  |  |  |  |  |  |  |  |  |  |  |  |  |  |  | □
54 □ |  |  |  |  |  |  |  |  |  |  |  |  |  |  |  |  |  |  |  | □
55 □ |  |  |  |  |  |  |  |  |  |  |  |  |  |  |  |  |  |  |  | □
56 □ |  |  |  |  |  |  |  |  |  |  |  |  |  |  |  |  |  |  |  | □
57 □ |  |  |  |  |  |  |  |  |  |  |  |  |  |  |  |  |  |  |  | □
58 □ |  |  |  |  |  |  |  |  |  |  |  |  |  |  |  |  |  |  |  | □
59 □ |  |  |  |  |  |  |  |  |  |  |  |  |  |  |  |  |  |  |  | □
60 □ |  |  |  |  |  |  |  |  |  |  |  |  |  |  |  |  |  |  |  | □
61 □ |  |  |  |  |  |  |  |  |  |  |  |  |  |  |  |  |  |  |  | □
62 □ |  |  |  |  |  |  |  |  |  |  |  |  |  |  |  |  |  |  |  | □
63 □ |  |  |  |  |  |  |  |  |  |  |  |  |  |  |  |  |  |  |  | □
64 □ |  |  |  |  |  |  |  |  |  |  |  |  |  |  |  |  |  |  |  | □
65 □ |  |  |  |  |  |  |  |  |  |  |  |  |  |  |  |  |  |  |  | □
66 □ |  |  |  |  |  |  |  |  |  |  |  |  |  |  |  |  |  |  |  | □
67 □ |  |  |  |  |  |  |  |  |  |  |  |  |  |  |  |  |  |  |  | □
68 □ |  |  |  |  |  |  |  |  |  |  |  |  |  |  |  |  |  |  |  | □
69 □ |  |  |  |  |  |  |  |  |  |  |  |  |  |  |  |  |  |  |  | □
70 □ |  |  |  |  |  |  |  |  |  |  |  |  |  |  |  |  |  |  |  | □
71 □ |  |  |  |  |  |  |  |  |  |  |  |  |  |  |  |  |  |  |  | □
72 □ |  |  |  |  |  |  |  |  |  |  |  |  |  |  |  |  |  |  |  | □
73 □ |  |  |  |  |  |  |  |  |  |  |  |  |  |  |  |  |  |  |  | □
74 □ |  |  |  |  |  |  |  |  |  |  |  |  |  |  |  |  |  |  |  | □
75 □ |  |  |  |  |  |  |  |  |  |  |  |  |  |  |  |  |  |  |  | □
76 □ |  |  |  |  |  |  |  |  |  |  |  |  |  |  |  |  |  |  |  | □
77 □ |  |  |  |  |  |  |  |  |  |  |  |  |  |  |  |  |  |  |  | □
78 □ |  |  |  |  |  |  |  |  |  |  |  |  |  |  |  |  |  |  |  | □
79 □ |  |  |  |  |  |  |  |  |  |  |  |  |  |  |  |  |  |  |  | □
80 □ |  |  |  |  |  |  |  |  |  |  |  |  |  |  |  |  |  |  |  | □
81 □ |  |  |  |  |  |  |  |  |  |  |  |  |  |  |  |  |  |  |  | □
82 □ |  |  |  |  |  |  |  |  |  |  |  |  |  |  |  |  |  |  |  | □
83 □ |  |  |  |  |  |  |  |  |  |  |  |  |  |  |  |  |  |  |  | □
84 □ |  |  |  |  |  |  |  |  |  |  |  |  |  |  |  |  |  |  |  | □
85 □ |  |  |  |  |  |  |  |  |  |  |  |  |  |  |  |  |  |  |  | □
86 □ |  |  |  |  |  |  |  |  |  |  |  |  |  |  |  |  |  |  |  | □
87 □ |  |  |  |  |  |  |  |  |  |  |  |  |  |  |  |  |  |  |  | □
88 □ |  |  |  |  |  |  |  |  |  |  |  |  |  |  |  |  |  |  |  | □
89 □ |  |  |  |  |  |  |  |  |  |  |  |  |  |  |  |  |  |  |  | □
90 □ |  |  |  |  |  |  |  |  |  |  |  |  |  |  |  |  |  |  |  | □
91 □ |  |  |  |  |  |  |  |  |  |  |  |  |  |  |  |  |  |  |  | □
92 □ |  |  |  |  |  |  |  |  |  |  |  |  |  |  |  |  |  |  |  | □
93 □ |  |  |  |  |  |  |  |  |  |  |  |  |  |  |  |  |  |  |  | □
94 □ |  |  |  |  |  |  |  |  |  |  |  |  |  |  |  |  |  |  |  | □
95 □ |  |  |  |  |  |  |  |  |  |  |  |  |  |  |  |  |  |  |  | □
96 □ |  |  |  |  |  |  |  |  |  |  |  |  |  |  |  |  |  |  |  | □
97 □ |  |  |  |  |  |  |  |  |  |  |  |  |  |  |  |  |  |  |  | □
98 □ |  |  |  |  |  |  |  |  |  |  |  |  |  |  |  |  |  |  |  | □
99 □ |  |  |  |  |  |  |  |  |  |  |  |  |  |  |  |  |  |  |  | □
100 □ |  |  |  |  |  |  |  |  |  |  |  |  |  |  |  |  |  |  |  | □
101 □ |  |  |  |  |  |  |  |  |  |  |  |  |  |  |  |  |  |  |  | □
102 □ |  |  |  |  |  |  |  |  |  |  |  |  |  |  |  |  |  |  |  | □
103 □ |  |  |  |  |  |  |  |  |  |  |  |  |  |  |  |  |  |  |  | □
104 □ |  |  |  |  |  |  |  |  |  |  |  |  |  |  |  |  |  |  |  | □
105 □ |  |  |  |  |  |  |  |  |  |  |  |  |  |  |  |  |  |  |  | □
106 □ |  |  |  |  |  |  |  |  |  |  |  |  |  |  |  |  |  |  |  | □
107 □ |  |  |  |  |  |  |  |  |  |  |  |  |  |  |  |  |  |  |  | □
108 □ |  |  |  |  |  |  |  |  |  |  |  |  |  |  |  |  |  |  |  | □
109 □ |  |  |  |  |  |  |  |  |  |  |  |  |  |  |  |  |  |  |  | □
110 □ |  |  |  |  |  |  |  |  |  |  |  |  |  |  |  |  |  |  |  | □
111 □ |  |  |  |  |  |  |  |  |  |  |  |  |  |  |  |  |  |  |  | □
112 □ |  |  |  |  |  |  |  |  |  |  |  |  |  |  |  |  |  |  |  | □
113 □ |  |  |  |  |  |  |  |  |  |  |  |  |  |  |  |  |  |  |  | □
114 □ |  |  |  |  |  |  |  |  |  |  |  |  |  |  |  |  |  |  |  | □
115 □ |  |  |  |  |  |  |  |  |  |  |  |  |  |  |  |  |  |  |  | □
116 □ |  |  |  |  |  |  |  |  |  |  |  |  |  |  |  |  |  |  |  | □
117 □ |  |  |  |  |  |  |  |  |  |  |  |  |  |  |  |  |  |  |  | □
118 □ |  |  |  |  |  |  |  |  |  |  |  |  |  |  |  |  |  |  |  | □
119 □ |  |  |  |  |  |  |  |  |  |  |  |  |  |  |  |  |  |  |  | □
120 □ |  |  |  |  |  |  |  |  |  |  |  |  |  |  |  |  |  |  |  | □
121 □ |  |  |  |  |  |  |  |  |  |  |  |  |  |  |  |  |  |  |  | □
122 □ |  |  |  |  |  |  |  |  |  |  |  |  |  |  |  |  |  |  |  | □
123 □ |  |  |  |  |  |  |  |  |  |  |  |  |  |  |  |  |  |  |  | □
124 □ |  |  |  |  |  |  |  |  |  |  |  |  |  |  |  |  |  |  |  | □
125 □ |  |  |  |  |  |  |  |  |  |  |  |  |  |  |  |  |  |  |  | □
126 □ |  |  |  |  |  |  |  |  |  |  |  |  |  |  |  |  |  |  |  | □
127 □ |  |  |  |  |  |  |  |  |  |  |  |  |  |  |  |  |  |  |  | □
128 □ |  |  |  |  |  |  |  |  |  |  |  |  |  |  |  |  |  |  |  | □
129 □ |  |  |  |  |  |  |  |  |  |  |  |  |  |  |  |  |  |  |  | □
130 □ |  |  |  |  |  |  |  |  |  |  |  |  |  |  |  |  |  |  |  | □
131 □ |  |  |  |  |  |  |  |  |  |  |  |  |  |  |  |  |  |  |  | □
132 □ |  |  |  |  |  |  |  |  |  |  |  |  |  |  |  |  |  |  |  | □
133 □ |  |  |  |  |  |  |  |  |  |  |  |  |  |  |  |  |  |  |  | □
134 □ |  |  |  |  |  |  |  |  |  |  |  |  |  |  |  |  |  |  |  | □
135 □ |  |  |  |  |  |  |  |  |  |  |  |  |  |  |  |  |  |  |  | □
136 □ |  |  |  |  |  |  |  |  |  |  |  |  |  |  |  |  |  |  |  | □
137 □ |  |  |  |  |  |  |  |  |  |  |  |  |  |  |  |  |  |  |  | □
138 □ |  |  |  |  |  |  |  |  |  |  |  |  |  |  |  |  |  |  |  | □
139 □ |  |  |  |  |  |  |  |  |  |  |  |  |  |  |  |  |  |  |  | □
140 □ |  |  |  |  |  |  |  |  |  |  |  |  |  |  |  |  |  |  |  | □
141 □ |  |  |  |  |  |  |  |  |  |  |  |  |  |  |  |  |  |  |  | □
142 □ |  |  |  |  |  |  |  |  |  |  |  |  |  |  |  |  |  |  |  | □
143 □ |  |  |  |  |  |  |  |  |  |  |  |  |  |  |  |  |  |  |  | □
144 □ |  |  |  |  |  |  |  |  |  |  |  |  |  |  |  |  |  |  |  | □
145 □ |  |  |  |  |  |  |  |  |  |  |  |  |  |  |  |  |  |  |  | □
146 □ |  |  |  |  |  |  |  |  |  |  |  |  |  |  |  |  |  |  |  | □
147 □ |  |  |  |  |  |  |  |  |  |  |  |  |  |  |  |  |  |  |  | □
148 □ |  |  |  |  |  |  |  |  |  |  |  |  |  |  |  |  |  |  |  | □
149 □ |  |  |  |  |  |  |  |  |  |  |  |  |  |  |  |  |  |  |  | □
150 □ |  |  |  |  |  |  |  |  |  |  |  |  |  |  |  |  |  |  |  | □
151 □ |  |  |  |  |  |  |  |  |  |  |  |  |  |  |  |  |  |  |  | □
152 □ |  |  |  |  |  |  |  |  |  |  |  |  |  |  |  |  |  |  |  | □
153 □ |  |  |  |  |  |  |  |  |  |  |  |  |  |  |  |  |  |  |  | □
154 □ |  |  |  |  |  |  |  |  |  |  |  |  |  |  |  |  |  |  |  | □
155 □ |  |  |  |  |  |  |  |  |  |  |  |  |  |  |  |  |  |  |  | □
156 □ |  |  |  |  |  |  |  |  |  |  |  |  |  |  |  |  |  |  |  | □
157 □ |  |  |  |  |  |  |  |  |  |  |  |  |  |  |  |  |  |  |  | □
158 □ |  |  |  |  |  |  |  |  |  |  |  |  |  |  |  |  |  |  |  | □
159 □ |  |  |  |  |  |  |  |  |  |  |  |  |  |  |  |  |  |  |  | □
160 □ |  |  |  |  |  |  |  |  |  |  |  |  |  |  |  |  |  |  |  | □
161 □ |  |  |  |  |  |  |  |  |  |  |  |  |  |  |  |  |  |  |  | □
162 □ |  |  |  |  |  |  |  |  |  |  |  |  |  |  |  |  |  |  |  | □
163 □ |  |  |  |  |  |  |  |  |  |  |  |  |  |  |  |  |  |  |  | □
164 □ |  |  |  |  |  |  |  |  |  |  |  |  |  |  |  |  |  |  |  | □
165 □ |  |  |  |  |  |  |  |  |  |  |  |  |  |  |  |  |  |  |  | □
166 □ |  |  |  |  |  |  |  |  |  |  |  |  |  |  |  |  |  |  |  | □
167 □ |  |  |  |  |  |  |  |  |  |  |  |  |  |  |  |  |  |  |  | □
168 □ |  |  |  |  |  |  |  |  |  |  |  |  |  |  |  |  |  |  |  | □
169 □ |  |  |  |  |  |  |  |  |  |  |  |  |  |  |  |  |  |  |  | □
170 □ |  |  |  |  |  |  |  |  |  |  |  |  |  |  |  |  |  |  |  | □
171 □ |  |  |  |  |  |  |  |  |  |  |  |  |  |  |  |  |  |  |  | □
172 □ |  |  |  |  |  |  |  |  |  |  |  |  |  |  |  |  |  |  |  | □
173 □ |  |  |  |  |  |  |  |  |  |  |  |  |  |  |  |  |  |  |  | □
174 □ |  |  |  |  |  |  |  |  |  |  |  |  |  |  |  |  |  |  |  | □
175 □ |  |  |  |  |  |  |  |  |  |  |  |  |  |  |  |  |  |  |  | □
176 □ |  |  |  |  |  |  |  |  |  |  |  |  |  |  |  |  |  |  |  | □
177 □ |  |  |  |  |  |  |  |  |  |  |  |  |  |  |  |  |  |  |  | □
178 □ |  |  |  |  |  |  |  |  |  |  |  |  |  |  |  |  |  |  |  | □
179 □ |  |  |  |  |  |  |  |  |  |  |  |  |  |  |  |  |  |  |  | □
180 □ |  |  |  |  |  |  |  |  |  |  |  |  |  |  |  |  |  |  |  | □
181 □ |  |  |  |  |  |  |  |  |  |  |  |  |  |  |  |  |  |  |  | □
182 □ |  |  |  |  |  |  |  |  |  |  |  |  |  |  |  |  |  |  |  | □
183 □ |  |  |  |  |  |  |  |  |  |  |  |  |  |  |  |  |  |  |  | □
184 □ |  |  |  |  |  |  |  |  |  |  |  |  |  |  |  |  |  |  |  | □
185 □ |  |  |  |  |  |  |  |  |  |  |  |  |  |  |  |  |  |  |  | □
186 □ |  |  |  |  |  |  |  |  |  |  |  |  |  |  |  |  |  |  |  | □
187 □ |  |  |  |  |  |  |  |  |  |  |  |  |  |  |  |  |  |  |  | □
188 □ |  |  |  |  |  |  |  |  |  |  |  |  |  |  |  |  |  |  |  | □
189 □ |  |  |  |  |  |  |  |  |  |  |  |  |  |  |  |  |  |  |  | □
190 □ |  |  |  |  |  |  |  |  |  |  |  |  |  |  |  |  |  |  |  | □
191 □ |  |  |  |  |  |  |  |  |  |  |  |  |  |  |  |  |  |  |  | □
192 □ |  |  |  |  |  |  |  |  |  |  |  |  |  |  |  |  |  |  |  | □
193 □ |  |  |  |  |  |  |  |  |  |  |  |  |  |  |  |  |  |  |  | □
194 □ |  |  |  |  |  |  |  |  |  |  |  |  |  |  |  |  |  |  |  | □
195 □ |  |  |  |  |  |  |  |  |  |  |  |  |  |  |  |  |  |  |  | □
196 □ |  |  |  |  |  |  |  |  |  |  |  |  |  |  |  |  |  |  |  | □
197 □ |  |  |  |  |  |  |  |  |  |  |  |  |  |  |  |  |  |  |  | □
198 □ |  |  |  |  |  |  |  |  |  |  |  |  |  |  |  |  |  |  |  | □
199 □ |  |  |  |  |  |  |  |  |  |  |  |  |  |  |  |  |  |  |  | □
200 □ |  |  |  |  |  |  |  |  |  |  |  |  |  |  |  |  |  |  |  | □
201 □ |  |  |  |  |  |  |  |  |  |  |  |  |  |  |  |  |  |  |  | □
202 □ |  |  |  |  |  |  |  |  |  |  |  |  |  |  |  |  |  |  |  | □
203 □ |  |  |  |  |  |  |  |  |  |  |  |  |  |  |  |  |  |  |  | □
204 □ |  |  |  |  |  |  |  |  |  |  |  |  |  |  |  |  |  |  |  | □
205 □ |  |  |  |  |  |  |  |  |  |  |  |  |  |  |  |  |  |  |  | □
206 □ |  |  |  |  |  |  |  |  |  |  |  |  |  |  |  |  |  |  |  | □
207 □ |  |  |  |  |  |  |  |  |  |  |  |  |  |  |  |  |  |  |  | □
208 □ |  |  |  |  |  |  |  |  |  |  |  |  |  |  |  |  |  |  |  | □
209 □ |  |  |  |  |  |  |  |  |  |  |  |  |  |  |  |  |  |  |  | □
210 □ |  |  |  |  |  |  |  |  |  |  |  |  |  |  |  |  |  |  |  | □
211 □ |  |  |  |  |  |  |  |  |  |  |  |  |  |  |  |  |  |  |  | □
212 □ |  |  |  |  |  |  |  |  |  |  |  |  |  |  |  |  |  |  |  | □
213 □ |  |  |  |  |  |  |  |  |  |  |  |  |  |  |  |  |  |  |  | □
214 □ |  |  |  |  |  |  |  |  |  |  |  |  |  |  |  |  |  |  |  | □
215 □ |  |  |  |  |  |  |  |  |  |  |  |  |  |  |  |  |  |  |  | □
216 □ |  |  |  |  |  |  |  |  |  |  |  |  |  |  |  |  |  |  |  | □
217 □ |  |  |  |  |  |  |  |  |  |  |  |  |  |  |  |  |  |  |  | □
218 □ |  |  |  |  |  |  |  |  |  |  |  |  |  |  |  |  |  |  |  | □
219 □ |  |  |  |  |  |  |  |  |  |  |  |  |  |  |  |  |  |  |  | □
220 □ |  |  |  |  |  |  |  |  |  |  |  |  |  |  |  |  |  |  |  | □
221 □ |  |  |  |  |  |  |  |  |  |  |  |  |  |  |  |  |  |  |  | □
222 □ |  |  |  |  |  |  |  |  |  |  |  |  |  |  |  |  |  |  |  | □
223 □ |  |  |  |  |  |  |  |  |  |  |  |  |  |  |  |  |  |  |  | □
224 □ |  |  |  |  |  |  |  |  |  |  |  |  |  |  |  |  |  |  |  | □
225 □ |  |  |  |  |  |  |  |  |  |  |  |  |  |  |  |  |  |  |  | □
226 □ |  |  |  |  |  |  |  |  |  |  |  |  |  |  |  |  |  |  |  | □
227 □ |  |  |  |  |  |  |  |  |  |  |  |  |  |  |  |  |  |  |  | □
228 □ |  |  |  |  |  |  |  |  |  |  |  |  |  |  |  |  |  |  |  | □
229 □ |  |  |  |  |  |  |  |  |  |  |  |  |  |  |  |  |  |  |  | □
230 □ |  |  |  |  |  |  |  |  |  |  |  |  |  |  |  |  |  |  |  | □
231 □ |  |  |  |  |  |  |  |  |  |  |  |  |  |  |  |  |  |  |  | □
232 □ |  |  |  |  |  |  |  |  |  |  |  |  |  |  |  |  |  |  |  | □
233 □ |  |  |  |  |  |  |  |  |  |  |  |  |  |  |  |  |  |  |  | □
234 □ |  |  |  |  |  |  |  |  |  |  |  |  |  |  |  |  |  |  |  | □
235 □ |  |  |  |  |  |  |  |  |  |  |  |  |  |  |  |  |  |  |  | □
236 □ |  |  |  |  |  |  |  |  |  |  |  |  |  |  |  |  |  |  |  | □
237 □ |  |  |  |  |  |  |  |  |  |  |  |  |  |  |  |  |  |  |  | □
238 □ |  |  |  |  |  |  |  |  |  |  |  |  |  |  |  |  |  |  |  | □
239 □ |  |  |  |  |  |  |  |  |  |  |  |  |  |  |  |  |  |  |  | □
240 □ |  |  |  |  |  |  |  |  |  |  |  |  |  |  |  |  |  |  |  | □
241 □ |  |  |  |  |  |  |  |  |  |  |  |  |  |  |  |  |  |  |  | □
242 □ |  |  |  |  |  |  |  |  |  |  |  |  |  |  |  |  |  |  |  | □
243 □ |  |  |  |  |  |  |  |  |  |  |  |  |  |  |  |  |  |  |  | □
244 □ |  |  |  |  |  |  |  |  |  |  |  |  |  |  |  |  |  |  |  | □
245 □ |  |  |  |  |  |  |  |  |  |  |  |  |  |  |  |  |  |  |  | □
246 □ |  |  |  |  |  |  |  |  |  |  |  |  |  |  |  |  |  |  |  | □
247 □ |  |  |  |  |  |  |  |  |  |  |  |  |  |  |  |  |  |  |  | □
248 □ |  |  |  |  |  |  |  |  |  |  |  |  |  |  |  |  |  |  |  | □
249 □ |  |  |  |  |  |  |  |  |  |  |  |  |  |  |  |  |  |  |  | □
250 □ |  |  |  |  |  |  |  |  |  |  |  |  |  |  |  |  |  |  |  | □
251 □ |  |  |  |  |  |  |  |  |  |  |  |  |  |  |  |  |  |  |  | □
252 □ |  |  |  |  |  |  |  |  |  |  |  |  |  |  |  |  |  |  |  | □
253 □ |  |  |  |  |  |  |  |  |  |  |  |  |  |  |  |  |  |  |  | □
254 □ |  |  |  |  |  |  |  |  |  |  |  |  |  |  |  |  |  |  |  | □
255 □ |  |  |  |  |  |  |  |  |  |  |  |  |  |  |  |  |  |  |  | □
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

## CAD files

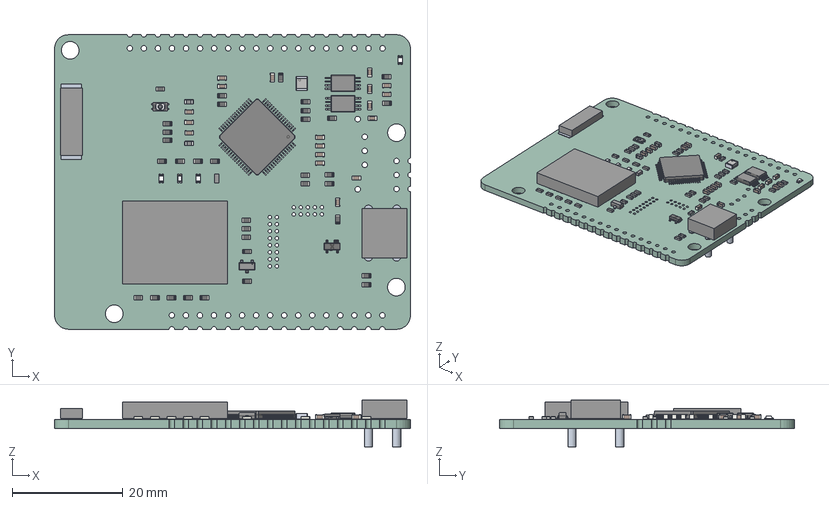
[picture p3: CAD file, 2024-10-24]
hardware/info/cad_model.step
64.4 x 53.3 x 8.42 mm
R_0603_1608Metric x 34
C_0603_1608Metric x 18
ASSEMBLY x 5
CSL1901UW1
PW0008A_ASM x 2
BLM18EG601SN1D x 2
XCL222B281ER-G
CSL1901MW1 x 3
R7FA6E2BB3CFM#BA0
SOT143B step
root
_autosave-balsun_PCB

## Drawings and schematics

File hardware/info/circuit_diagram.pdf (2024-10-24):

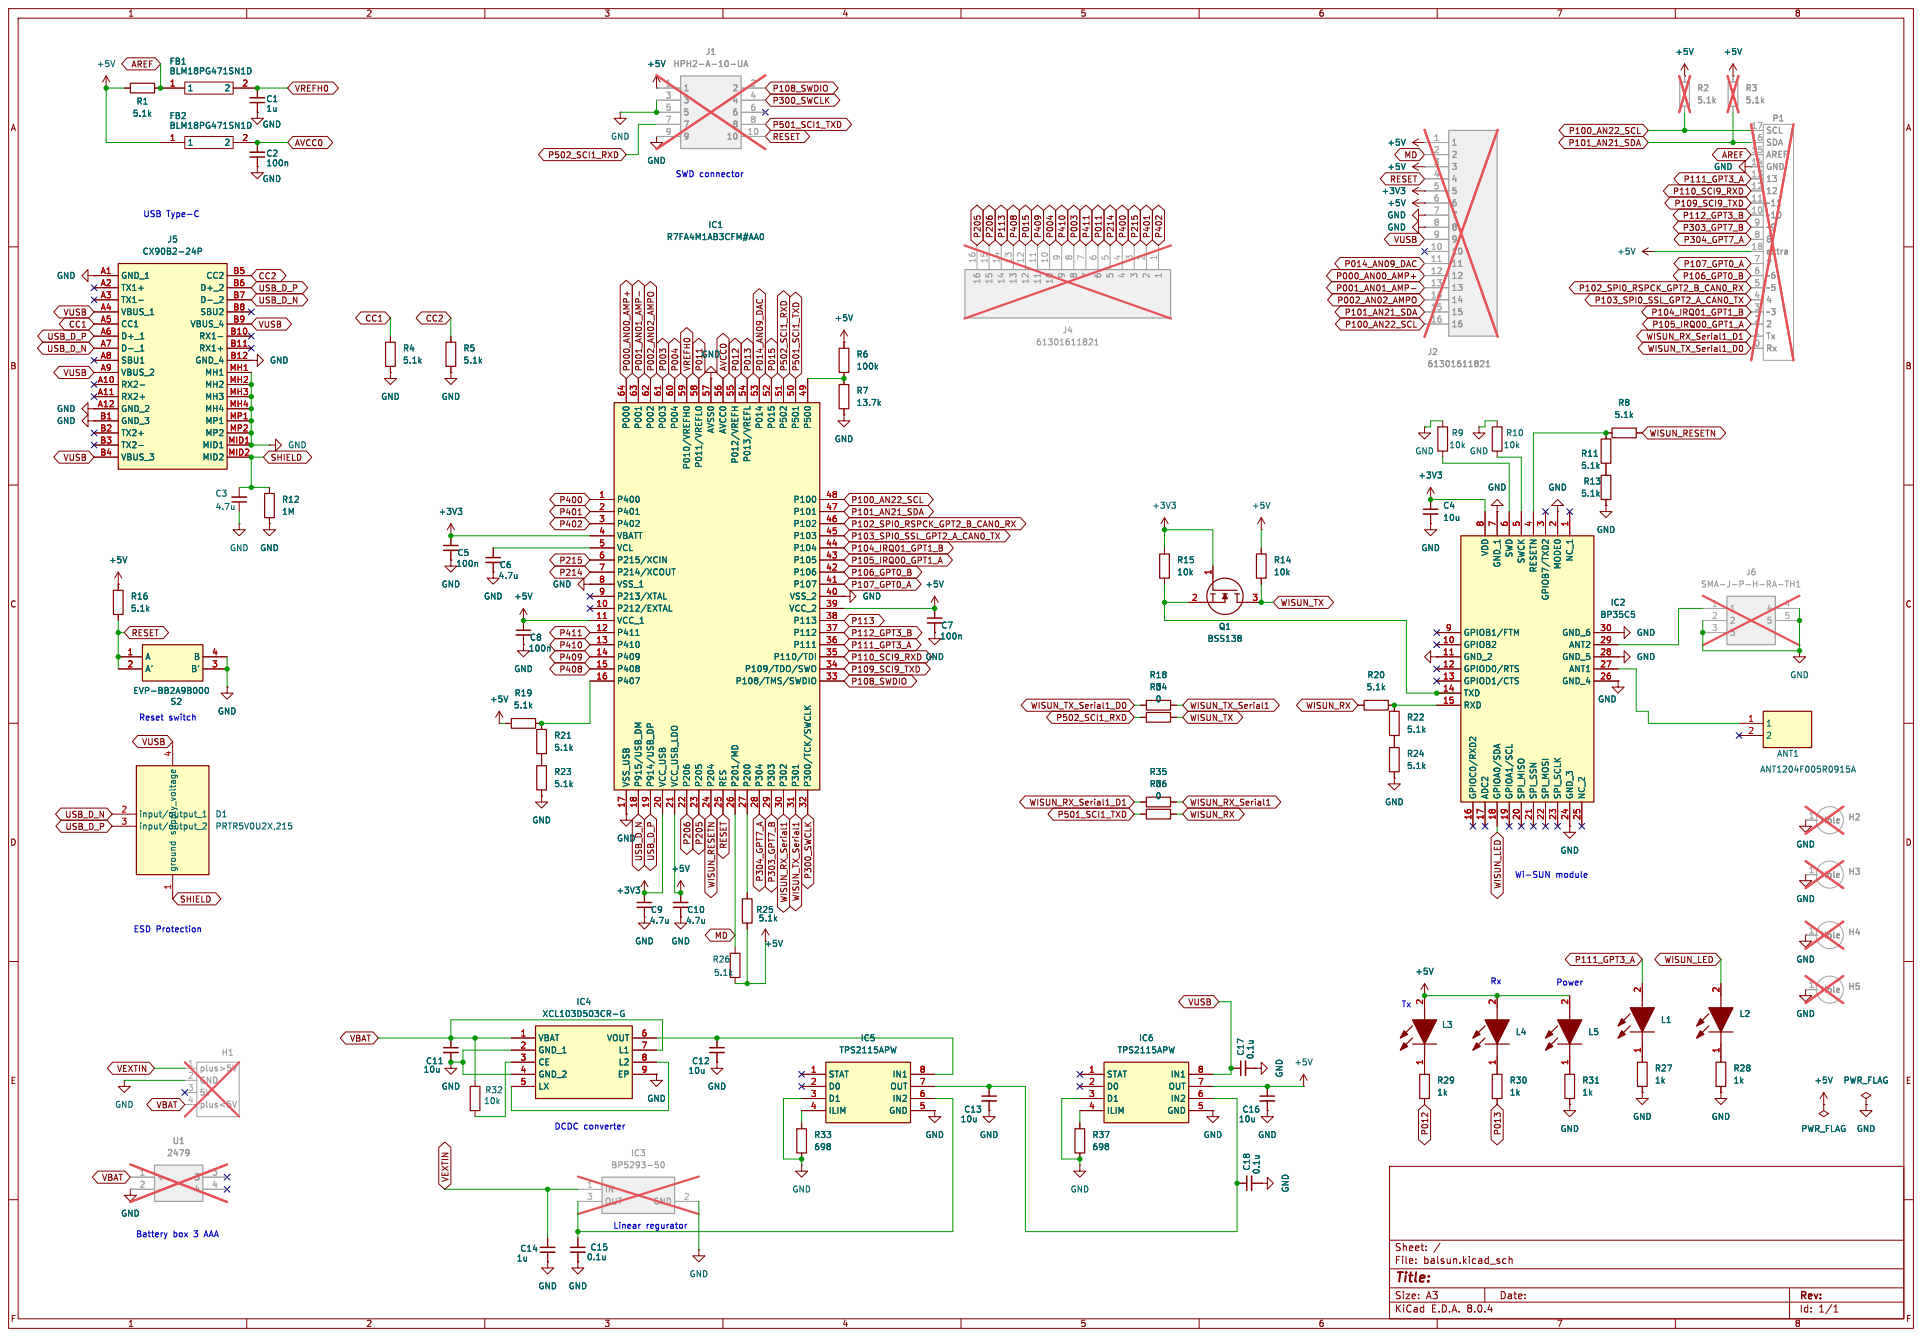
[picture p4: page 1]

9 GND GND GND GND

61301611821 GND GND GND GND

1 GPIOB2 10 GND_2 11 GPIOD0/RTS 12 GPIOD1/CTS 13 TXD 14 RXD 15 GPIOC0/RXD2 16 ADC2 17 GPIOA0/SDA 18 GPIOA1/SCL 19 MODE0

Power Battery box 3 AAA

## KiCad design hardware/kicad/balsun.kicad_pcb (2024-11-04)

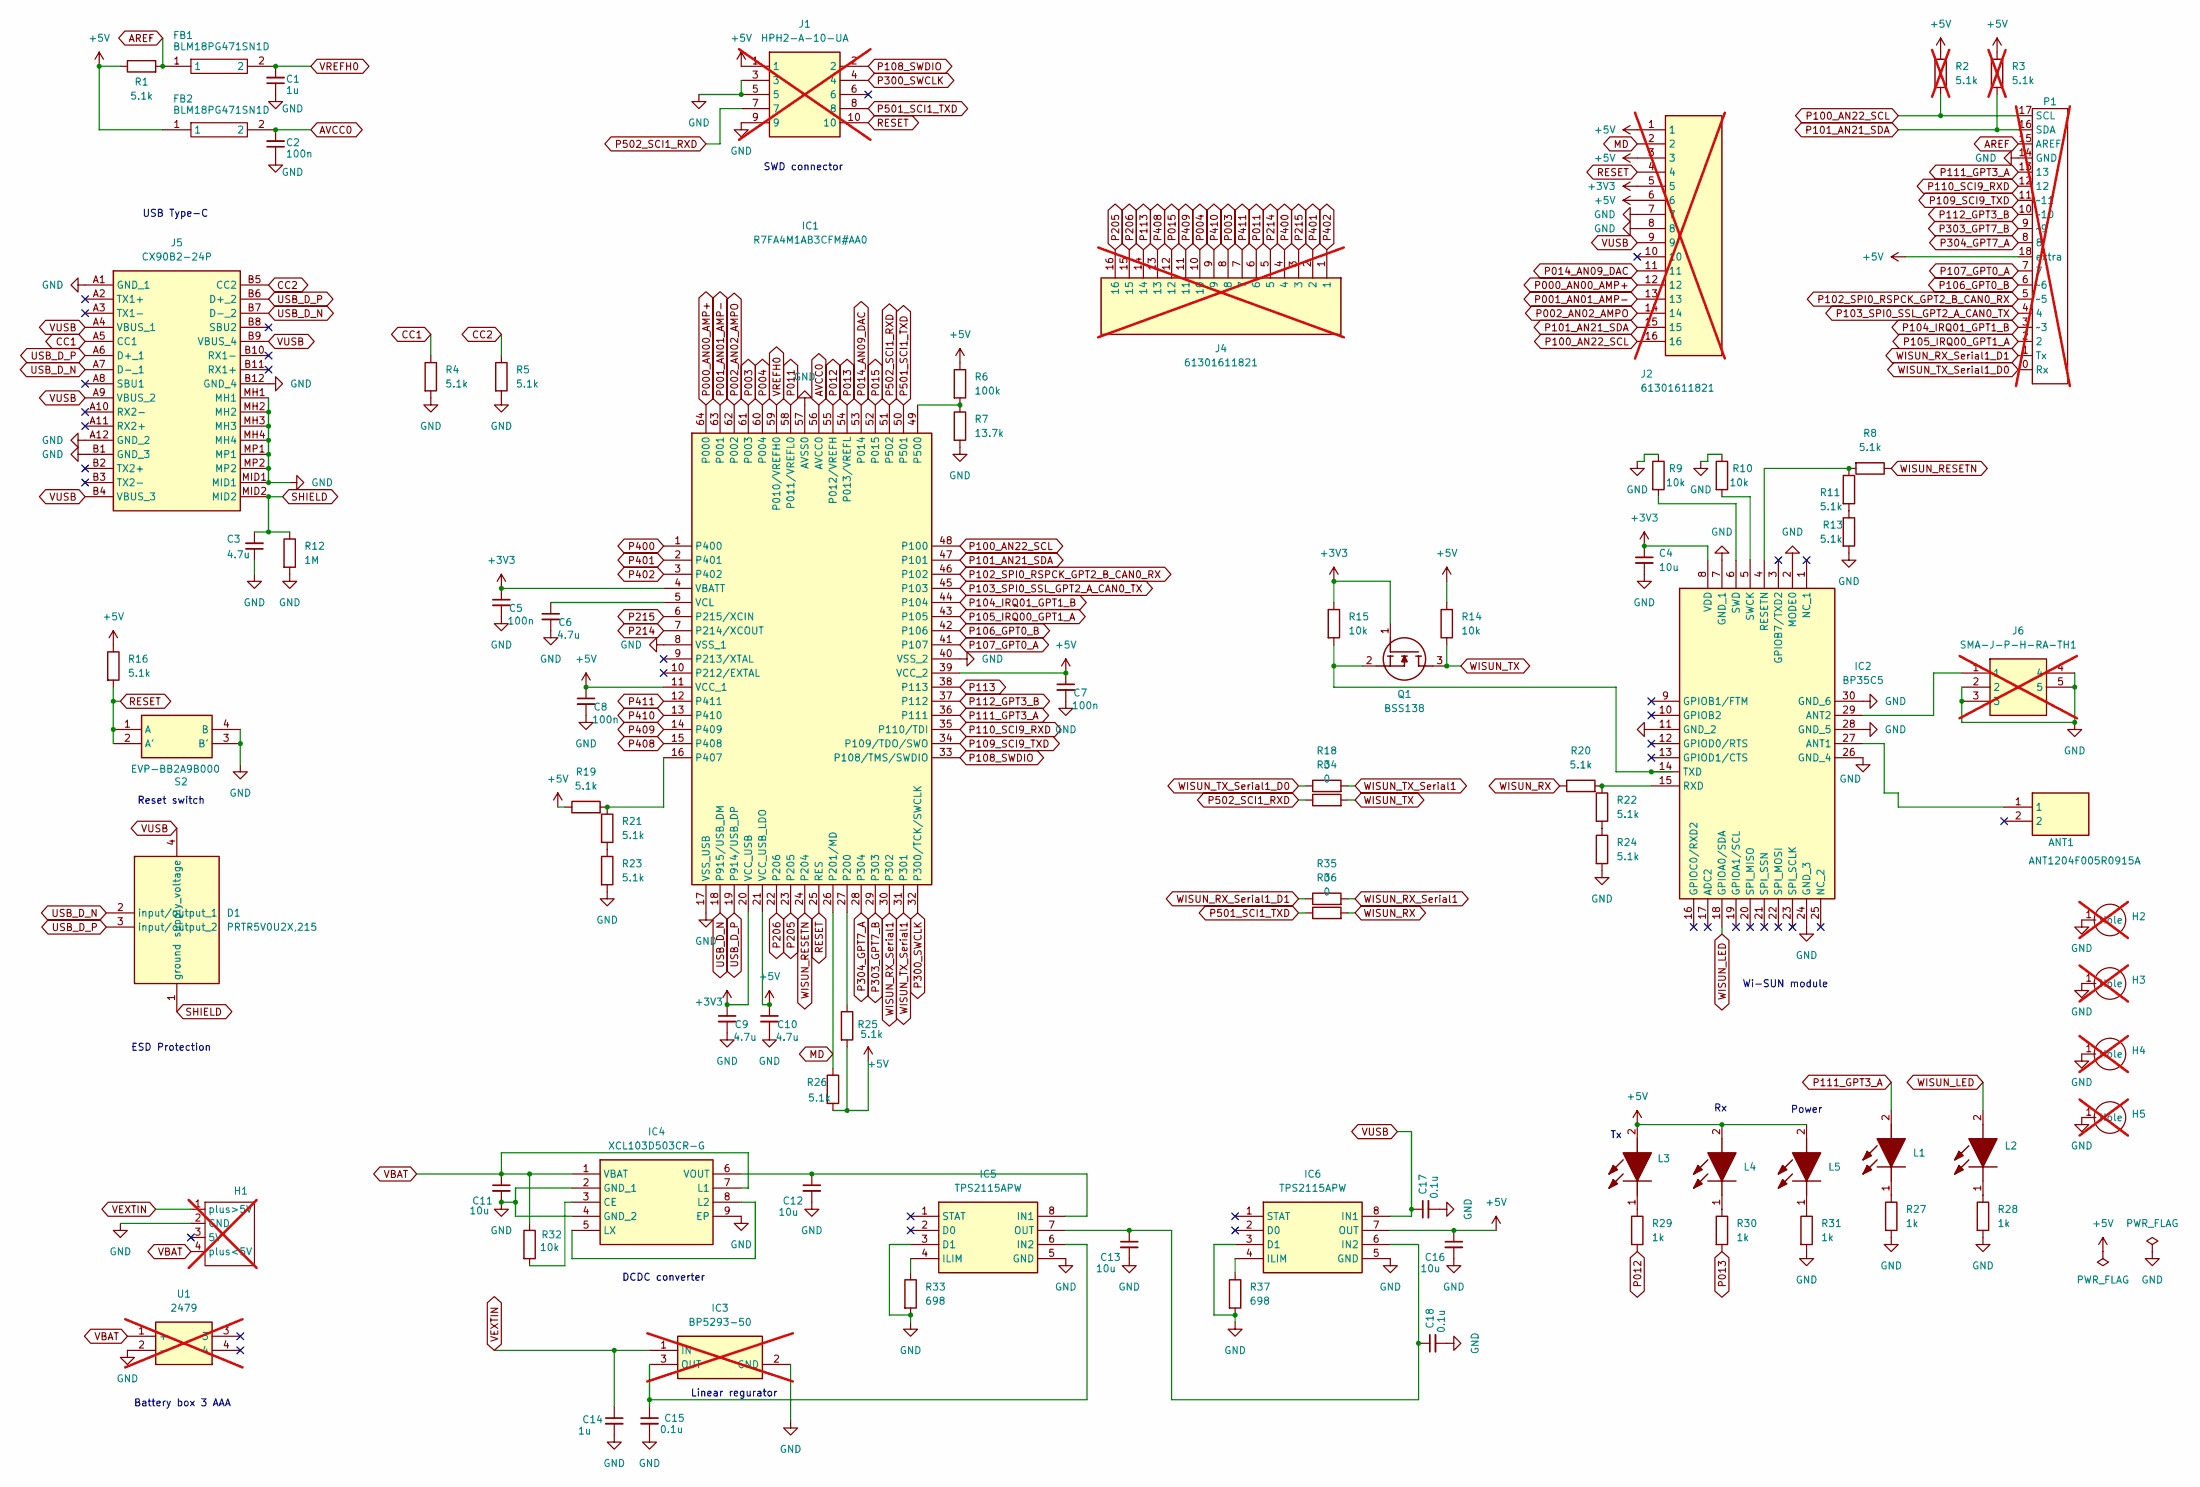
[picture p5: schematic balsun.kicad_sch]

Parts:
ANT1: ANT1204F005R0915A; Manufacturer_Part_Number ANT1204F005R0915A; Mouser Part Number 603-ANT1204F005R0915
C1, C14: 1u; C_0603_1608Metric; Mouser Part Number 603-CC603KRX5R6BB105
C2, C5, C7, C8: 100n; C_0603_1608Metric; Mouser Part Number 603-CC603KRX7R6BB104
C3, C6, C9, C10: 4.7u; C_0603_1608Metric; Mouser Part Number 603-CC603ZRY5V6BB475
C4, C11, C12, C13, C16: 10u; C_0603_1608Metric; Mouser Part Number 603-CC603MRX6S6BB106
C15, C17, C18: 0.1u; C_0603_1608Metric; Mouser Part Number 603-CC603KRX7R6BB104
D1: PRTR5V0U2X,215; PRTR5V0U2X; Manufacturer_Part_Number PRTR5V0U2X,215; Mouser Part Number 771-PRTR5V0U2X-T/R
FB1, FB2: BLM18PG471SN1D; BLM18SP221SN1B; Manufacturer_Part_Number BLM18PG471SN1D; Mouser Part Number 81-BLM18PG471SN1D
H1: power_holes; not fitted
H2, H3, H4, H5: MountingHole_3.2mm_M3; not fitted
IC1: R7FA4M1AB3CFM#AA0; QFP50P1200X1200X170-64N; Manufacturer_Part_Number R7FA4M1AB3CFM#AA0; Mouser Part Number 968-7FA4M1AB3CFM#AA0
IC2: BP35C5; Manufacturer_Part_Number BP35C5; Mouser Part Number 755-BP35C5
IC3: BP5293-50; not fitted
IC4: XCL103D503CR-G; XCL103D503CRG; Manufacturer_Part_Number XCL103D503CR-G; Mouser Part Number 865-XCL103D503CR-G
IC5, IC6: TPS2115APW; SOP65P640X120-8N; Manufacturer_Part_Number TPS2115APW; Mouser Part Number 595-TPS2115APW
J1: HPH2-A-10-UA; HDRV10W45P127_2X5_635X345X400P; Manufacturer_Part_Number HPH2-A-10-UA; Mouser Part Number 737-HPH2-A-10-UA; not fitted
J2: 61301611821; arduino_pins_2; Manufacturer_Part_Number 61301611821; Mouser Part Number 710-61301611821; not fitted
J4: 61301611821; HDRV16; Manufacturer_Part_Number 61301611821; Mouser Part Number 710-61301611821; not fitted
J5: CX90B2-24P; CX90B224P; Manufacturer_Part_Number CX90B2-24P; Mouser Part Number 798-CX90B2-24P
J6: SMA-J-P-H-RA-TH1; CON-SMA-EDGE-S; Manufacturer_Part_Number SMA-J-P-H-RA-TH1; Mouser Part Number 710-63012202124505; not fitted
L1, L2, L5: SML-P11UTT86; CSL1901MW1; Manufacturer_Part_Number SML-P11UTT86; Mouser Part Number 755-755-SML-P11UTT86
L3: SML-P11UTT86; CSL1901YW1; Manufacturer_Part_Number SML-P11UTT86; Mouser Part Number 755-755-SML-P11UTT86
L4: SML-P11UTT86; CSL1901UW1; Manufacturer_Part_Number SML-P11UTT86; Mouser Part Number 755-755-SML-P11UTT86
P1: arduino_pins1; not fitted
Q1: BSS138; SOT95P240X120-3N; Manufacturer_Part_Number BSS138; Mouser Part Number 512-BSS138
R1, R4, R5, R8, R11, R13, R16, R19, R20, R21, R22, R23, R24, R25, R26: 5.1k; R_0603_1608Metric; Mouser Part Number 667-ERA-3ARB512V
R2, R3: 5.1k; R_0603_1608Metric; Mouser Part Number 667-ERA-3ARB512V; not fitted
R6: 100k; R_0603_1608Metric; Mouser Part Number 667-ERA-3AEB104V
R7: 13.7k; R_0603_1608Metric; Mouser Part Number 667-ERA-3AEB1372V
R9, R10, R32: 10k; R_0603_1608Metric; Mouser Part Number 667-ERA-3ARB103V
R12: 1M; R_0603_1608Metric; Mouser Part Number 667-ERJ-3EKF1004V
R14, R15: 10k; R_0603_1608Metric; Mouser Part Number 667-ERA-3ARB512V
R18, R34, R35, R36: 0; R_0603_1608Metric; Mouser Part Number 667-ERJ-3GEY0R00V
R27, R28, R29, R30, R31: 1k; R_0603_1608Metric; Mouser Part Number 667-ERJ-U03J331V
R33, R37: 698; R_0603_1608Metric; Mouser Part Number 667-ERA-3AEB6980V
S2: EVP-BB2A9B000; EVPBB2A9B000; Manufacturer_Part_Number EVP-BB2A9B000; Mouser Part Number 667-EVP-BB2A9B000
U1: 2479; Manufacturer_Part_Number 2479; Mouser Part Number 534-2479; not fitted

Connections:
+3V3: C4.1, C5.1, C9.1, IC1.4 (VBATT), IC1.20 (VCC_USB), IC2.8 (VDD), J2.5, Q1.1 (G), R15.1
+5V: C7.1, C8.1, C10.1, C16.1, FB2.1, IC1.11 (VCC_1), IC1.21 (VCC_USB_LDO), IC1.39 (VCC_2), IC6.7 (OUT), J1.1, J2.1, J2.3, J2.6, L3.2 (A), L4.2 (A), L5.2 (A), P1.18 (extra), R1.1, R2.1, R3.1, R6.1, R14.2, R16.1, R19.1, R25.2, R26.2
AREF: FB1.1, P1.15 (AREF), R1.2
AVCC0: C2.2, FB2.2, IC1.56 (AVCC0)
CC1: J5.A5 (CC1), R4.1
CC2: J5.B5 (CC2), R5.1
GND: C1.1, C2.1, C3.1, C4.2, C5.2, C6.2, C7.2, C8.2, C9.2, C10.2, C11.2, C12.2, C13.2, C14.2, C15.2, C16.2, C17.2, C18.2, H1.2 (GND), H2.1 (Hole), H3.1 (Hole), H4.1 (Hole), H5.1 (Hole), IC1.8 (VSS_1), IC1.17 (VSS_USB), IC1.40 (VSS_2), IC1.57 (AVSS0), IC2.2 (MODE0), IC2.7 (GND_1), IC2.11 (GND_2), IC2.24 (GND_3), IC2.26 (GND_4), IC2.28 (GND_5), IC2.30 (GND_6), IC3.2 (GND), IC4.2 (GND_1), IC4.4 (GND_2), IC4.9 (EP), IC5.3 (D1), IC5.5 (GND), IC6.3 (D1), IC6.5 (GND), J1.3, J1.5, J1.9, J2.7, J2.8, J5.A1 (GND_1), J5.A12 (GND_2), J5.B1 (GND_3), J5.B12 (GND_4), J5.MH1, J5.MH2, J5.MH3, J5.MH4, J5.MID1, J5.MP1, J5.MP2, J6.2, J6.3, J6.4, J6.5, P1.14 (GND), R4.2, R5.2, R7.2, R9.1, R10.1, R12.2, R13.2, R23.2, R24.2, R27.2, R28.2, R31.2, R33.2, R37.2, S2.3 (B'), S2.4 (B), U1.2 (-)
MD: IC1.26 (P201/MD), J2.2, R26.1
unnamed: IC1.27 (P200), R25.1
unnamed: IC1.16 (P407), R19.2, R21.1
unnamed: IC1.49 (P500), R6.2, R7.1
unnamed: C6.1, IC1.5 (VCL)
unnamed: ANT1.1, IC2.27 (ANT1)
unnamed: IC2.29 (ANT2), J6.1
unnamed: IC2.4 (RESETN), R8.2, R11.1
unnamed: IC2.15 (RXD), R20.2, R22.1
unnamed: IC2.5 (SWCK), R10.2
unnamed: IC2.6 (SWD), R9.2
unnamed: IC2.14 (TXD), Q1.2 (S), R15.2
unnamed: C15.1, IC3.3 (OUT), IC5.6 (IN2)
unnamed: IC4.3 (CE), R32.2
unnamed: IC4.5 (LX), IC4.8 (L2)
unnamed: C12.1, IC4.6 (VOUT), IC5.8 (IN1)
unnamed: IC5.4 (ILIM), R33.1
unnamed: C13.1, C18.1, IC5.7 (OUT), IC6.6 (IN2)
unnamed: IC6.4 (ILIM), R37.1
unnamed: L1.1 (K), R27.1
unnamed: L2.1 (K), R28.1
unnamed: L3.1 (K), R29.1
unnamed: L4.1 (K), R30.1
unnamed: L5.1 (K), R31.1
unnamed: R11.2, R13.1
unnamed: R21.2, R23.1
unnamed: R22.2, R24.1
P000_AN00_AMP+: IC1.64 (P000), J2.12
P001_AN01_AMP-: IC1.63 (P001), J2.13
P002_AN02_AMPO: IC1.62 (P002), J2.14
P003: IC1.61 (P003), J4.8
P004: IC1.60 (P004), J4.10
P011: IC1.58 (P011/VREFL0), J4.6
P012: IC1.55 (P012/VREFH), R29.2
P013: IC1.54 (P013/VREFL), R30.2
P014_AN09_DAC: IC1.53 (P014), J2.11
P015: IC1.52 (P015), J4.12
P100_AN22_SCL: IC1.48 (P100), J2.16, P1.17 (SCL), R2.2
P101_AN21_SDA: IC1.47 (P101), J2.15, P1.16 (SDA), R3.2
P102_SPI0_RSPCK_GPT2_B_CAN0_RX: IC1.46 (P102), P1.5 (~5)
P103_SPI0_SSL_GPT2_A_CAN0_TX: IC1.45 (P103), P1.4
P104_IRQ01_GPT1_B: IC1.44 (P104), P1.3 (~3)
P105_IRQ00_GPT1_A: IC1.43 (P105), P1.2
P106_GPT0_B: IC1.42 (P106), P1.6 (~6)
P107_GPT0_A: IC1.41 (P107), P1.7
P108_SWDIO: IC1.33 (P108/TMS/SWDIO), J1.2
P109_SCI9_TXD: IC1.34 (P109/TDO/SWO), P1.11 (~11)
P110_SCI9_RXD: IC1.35 (P110/TDI), P1.12
P111_GPT3_A: IC1.36 (P111), L1.2 (A), P1.13
P112_GPT3_B: IC1.37 (P112), P1.10 (~10)
P113: IC1.38 (P113), J4.14
P205: IC1.23 (P205), J4.16
P206: IC1.22 (P206), J4.15
P214: IC1.7 (P214/XCOUT), J4.5
P215: IC1.6 (P215/XCIN), J4.3
P300_SWCLK: IC1.32 (P300/TCK/SWCLK), J1.4
P303_GPT7_B: IC1.29 (P303), P1.9 (~9)
P304_GPT7_A: IC1.28 (P304), P1.8
P400: IC1.1 (P400), J4.4
P401: IC1.2 (P401), J4.2
P402: IC1.3 (P402), J4.1
P408: IC1.15 (P408), J4.13
P409: IC1.14 (P409), J4.11
P410: IC1.13 (P410), J4.9
P411: IC1.12 (P411), J4.7
P501_SCI1_TXD: IC1.50 (P501), J1.8, R36.1
P502_SCI1_RXD: IC1.51 (P502), J1.7, R34.1
RESET: IC1.25 (RES), J1.10, J2.4, R16.2, S2.1 (A), S2.2 (A')
SHIELD: C3.2, D1.1 (ground), J5.MID2, R12.1
USB_D_N: D1.2 (input/output_1), IC1.18 (P915/USB_DM), J5.A7 (D-_1), J5.B7 (D-_2)
USB_D_P: D1.3 (input/output_2), IC1.19 (P914/USB_DP), J5.A6 (D+_1), J5.B6 (D+_2)
VBAT: C11.1, H1.4 (plus<5V), IC4.1 (VBAT), IC4.7 (L1), R32.1, U1.1 (+)
VEXTIN: C14.1, H1.1 (plus>5V), IC3.1 (IN)
VREFH0: C1.2, FB1.2, IC1.59 (P010/VREFH0)
VUSB: C17.1, D1.4 (supply_voltage), IC6.8 (IN1), J2.9, J5.A4 (VBUS_1), J5.A9 (VBUS_2), J5.B4 (VBUS_3), J5.B9 (VBUS_4)
WISUN_LED: IC2.18 (GPIOA0/SDA), L2.2 (A)
WISUN_RESETN: IC1.24 (P204), R8.1
WISUN_RX: R20.1, R36.2
WISUN_RX_Serial1: IC1.30 (P302), R35.2
WISUN_RX_Serial1_D1: P1.1 (Tx), R35.1
WISUN_TX: Q1.3 (D), R14.1, R34.2
WISUN_TX_Serial1: IC1.31 (P301), R18.2
WISUN_TX_Serial1_D0: P1.0 (Rx), R18.1

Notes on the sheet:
Reset switch
USB Type-C
Power
SWD connector
Wi-SUN module
ESD Protection
DCDC converter
Linear regurator
Battery box 3 AAA

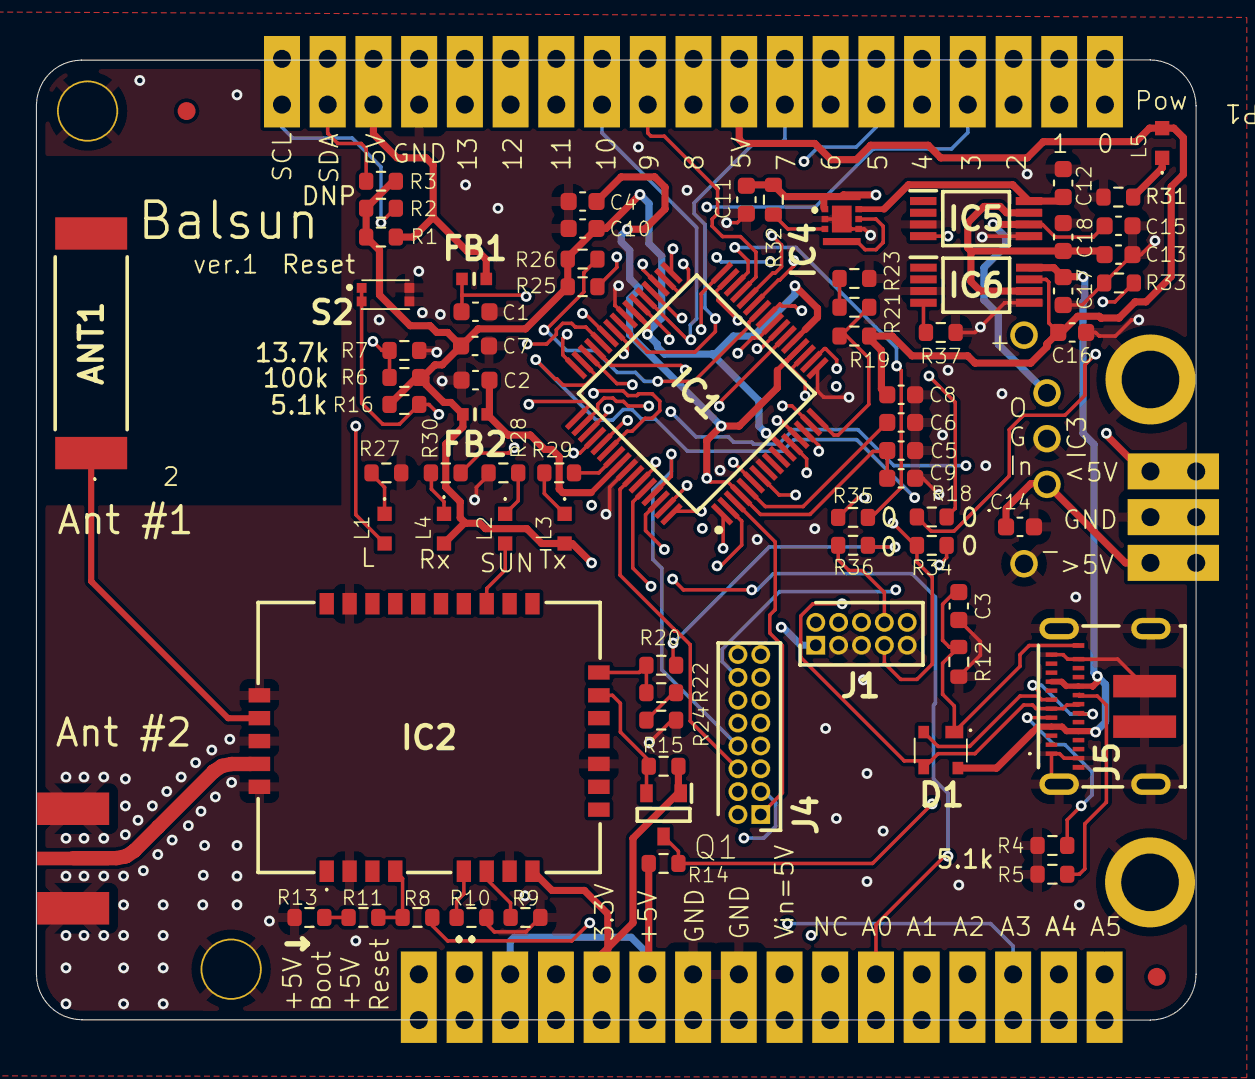
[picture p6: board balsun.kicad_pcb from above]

Board: 4 copper layers, 64.4 x 53.3 mm, 83 parts (1 on the bottom side), 90 nets.

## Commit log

2024-10-24 Add KiCAD files
    [balsun.kicad_pcb, balsun.kicad_sch]
2024-10-24 Add design information
    [BOM.csv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]
2024-10-24 add view files
    [cad_model.step]
2024-10-24 add license for arduino example
2024-10-28 Add grouped BOMs
    [BOM_grouped.csv, BOM_pban.xlsx]
2024-11-01 update BOM for p-ban.com
    [BOM_pban.xlsx]
2024-11-04 update pattern
    [balsun-B_Cu.gbr, balsun-B_Mask.gbr, balsun-B_Silks.gbr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]
2024-11-04 update photo
    [balsun.kicad_sch]
